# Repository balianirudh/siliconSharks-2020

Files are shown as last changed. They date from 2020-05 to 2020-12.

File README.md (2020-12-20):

# Silicon Sharks ROV 2020

The Silicon Sharks are a high school robotics team that participate in the MATE underwater robotics competition. As a team, our mission is to develop a remotely operated vehicle (ROV) that is capable of exploring public waterways with features for drivers to easily perform tasks and collect data. The five-person team worked together to create this ROV. The Silicon Sharks have three separate subteams (design, electrical, and software) that each played a key role in developing the ROV. My role on the 2020 team was to lead the design and electrical subteams.

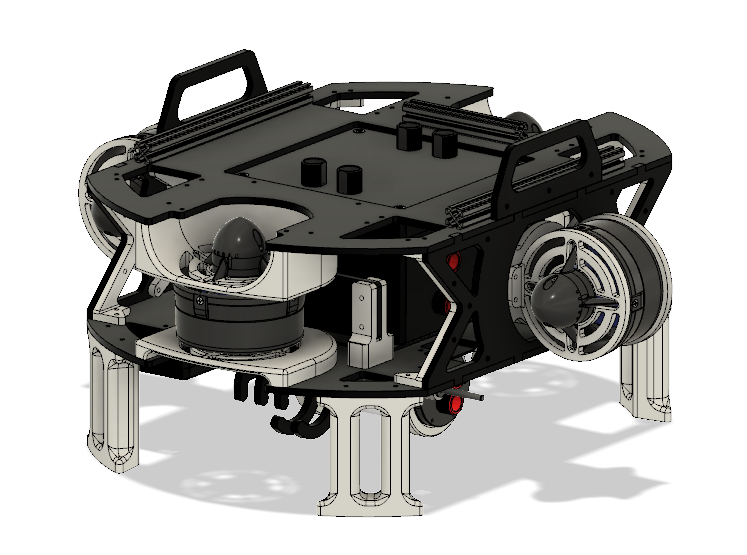
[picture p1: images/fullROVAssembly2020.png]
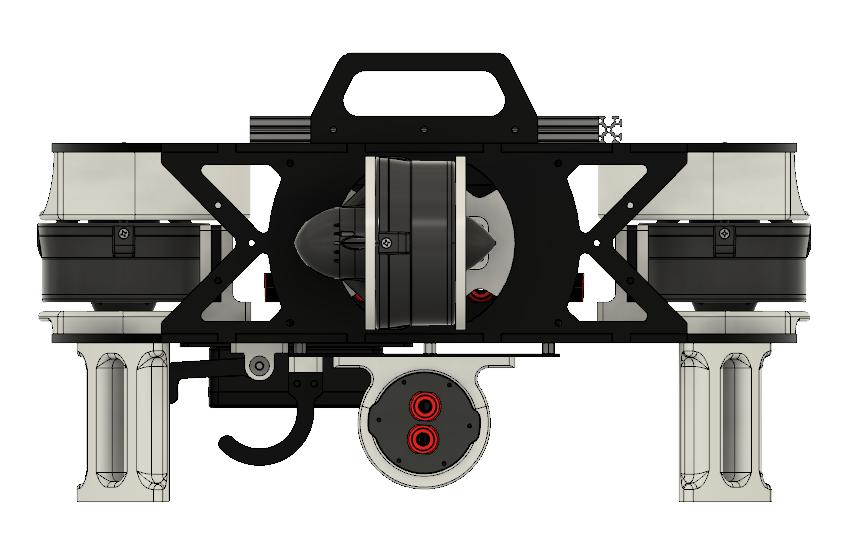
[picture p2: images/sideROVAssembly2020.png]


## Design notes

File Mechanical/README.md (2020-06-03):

# Mechanical Subsystems

The ROV is made up of several mechanical subsystems. The primary mechanical systems of the ROV are the frame, the main electronics
enclosure, the camera enclosures, and the gripper. Our goal was to make a neutrally buoyant, compact, and easily-assembled ROV. To do this, there was a constant emphasis on original design and exploiting custom fabrication.

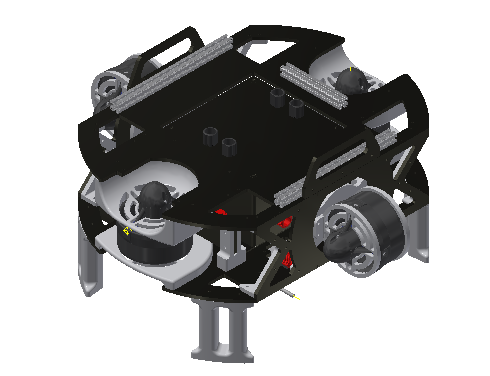
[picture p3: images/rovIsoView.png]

<p align="center"> Isometric View of ROV </p>
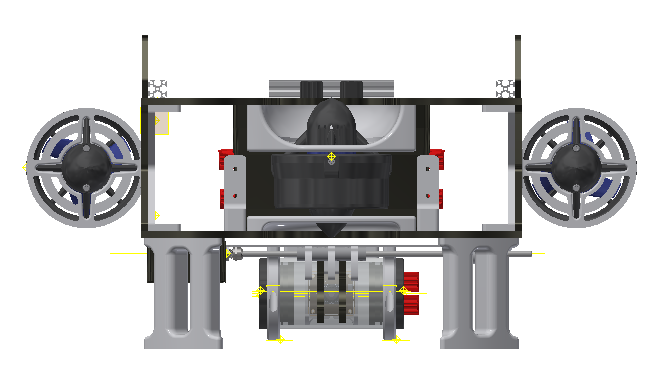
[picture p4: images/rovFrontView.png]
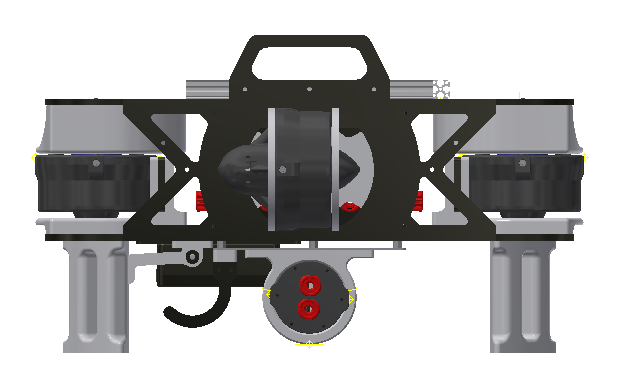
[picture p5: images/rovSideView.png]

<p align="center"> Front View of ROV (left), Side View of ROV (right) </p>

## Frame

When designing the frame of the ROV, the focus was put on creating a high strenth, lightweight, customizable structure with room for adaptability and expasion. The frame was produced thorugh addititive manufacturing (3D printing) due to its rapid prototyping capabilities and ease of customizable. PLA plastic was the primary plastic used for manufacturing because it was a plastic that was not only strong enough, but it is safe to use in underwater applications.

The parts that make up the frame are connected in several ways. The main way is through brackets that are soley meant to bring a general structure to the frame. From here, specific parts such as the main electronics housing or thruster guards reinforce the frame while serving different purposes altogether.

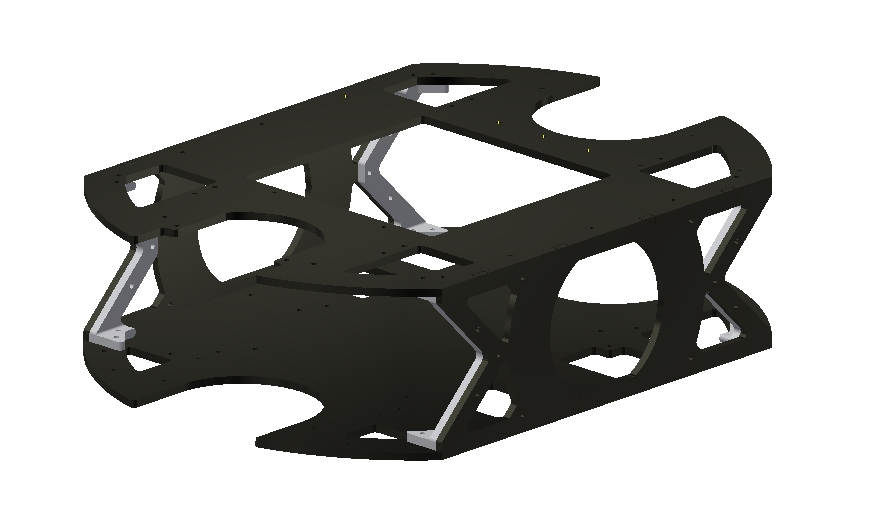
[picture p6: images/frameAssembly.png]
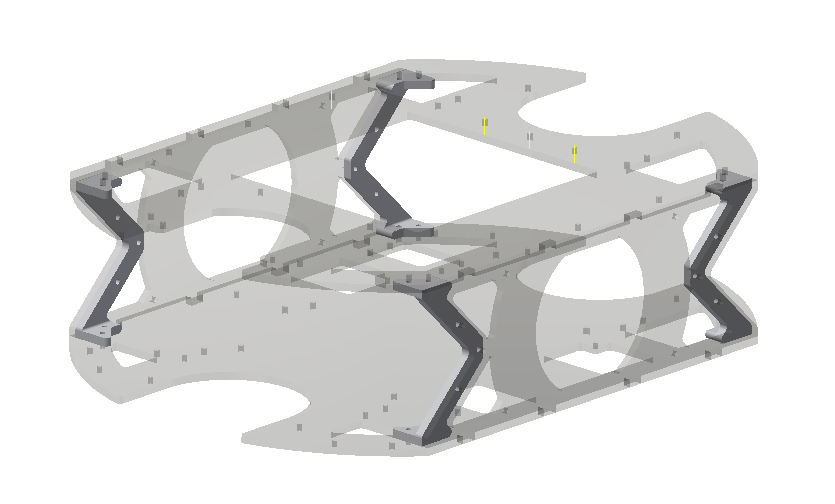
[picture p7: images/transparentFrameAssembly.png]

<p align="center">Frame Assembly</p>

In the process of desiging the frame, considerations had to made for the propulsion of the ROV. The team was constrainted to four thrusters. With these four thrusters, the team had to maximize the ROV's degrees of freedom. The way this was done is discussed in the next section.

## Propulsion

As stated before, the team was constrained to four thrusters. This constraint stems from the regulations of the MATE competition and the thrusters chosen for this ROV. For safety reasons, teams participating in the Ranger class are limited to a 25 amp power supply. The thrusters chosen for this ROV were the Blue Robotics T200 thruster. This thruster was chosen because of its force to current ratio and relative affordability.

"screenshot of force vs current graph of thruster"

Knowing that the power supply can only supply 25 amps, in the electrical design, 20 amps was allocated to the propulsion system. This maximizes the current dedicated to thrusters while leaving enough current for other electrical components and a safety buffer to avoid blowing a fuse. Maximizing the total thrust force is advantageous for obvious reasons. It would provide the maximum agility and make the ROV practical for real-world applications.

The final design was between a three thruster configuration or a four thruster configuration. The team opted for the four thrsuter configuration because of its higher total thrust, but more importantly its symmetry resulting in better controllability. The thruster configuration consists of two thrusters dedicated for vertical movement (z-axis) and two thrusters dedicated for lateral movement (xy plane). This thruster configuration with the thrusters ability to produce a thrust in either direction gives the ROV control over its pitch and yaw. However, the ROV doesn't have explicit control of its roll. Buoyancy foam placed on the top of the ROV keeps it upright and prevents it from rolling. 

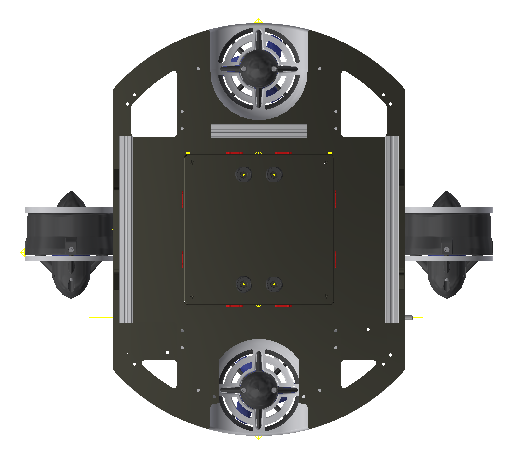
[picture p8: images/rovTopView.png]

<p align="center"> Top View of ROV that highlights thruster configuration</p>

In a future iteration of this ROV, the team plans to gimbal the two thrusters dedicated for lateral movement. This will allow the ROV to move on more complicated paths giving the ROV greater freedom in the water.

## Electronic Enclosures & Sealing

### Main Enclosure

The main electronics enclosure is a diecast aluminum enclosure produced by Polycase. The enclosure is a 6.5in box that houses all the main electronics for communication and thruster control. The diecast aluminum is non-porus and high strength to ensure that the material won't allow water to move into the box over long periods of time submerged in water and won't deform under the water pressures we expect to face.

The electronics within the box are accessed by opening the lid of the enclosure that is held down by four screws. The screws ensure that the lid does not move and keeps the face seal O-ring compressed.

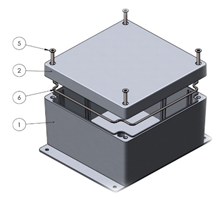
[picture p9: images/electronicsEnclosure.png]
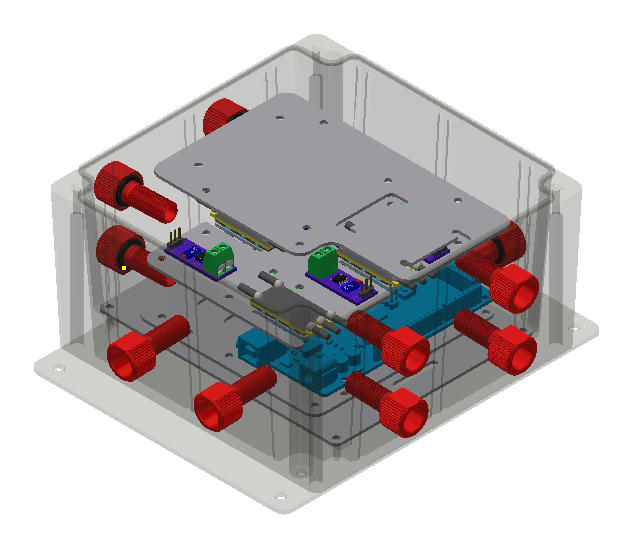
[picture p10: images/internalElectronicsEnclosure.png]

<p align="center"> AN-10F enclosure from Polycase (left), Interior ellectronics enclosure assembly (right) </p>

### Camera Enclosure

The camera enclosure is made up of a clear acrylic tube, two aluminum flanges, and two endcaps. The aluminum flanges allow for the endcaps to mount to the acrylic tube in a way that creates a water-tight seal. Each aluminum flange has two bore O-rings and one face seal O-ring. The acrylic tube compresses the bore O-rings when the flange is inserted and the endcap compresses the face seal O-ring. Clear acrylic tubes were used for the camera enclosures because they make it easy to adjust the camera angle while leaving a wide, unobstructed view for the camera.

"add pictures of camera enclosure"

### Cable Routing

To move cables in and out of the electronics enclosures (with exception to the cameras), aluminum cable penetrators were used. A face seal O-ring on the outside made a water-tight seal with the face of the electronics enclosure while washers inside along with a nut hold the penetrator in place. The cables are secured inside the penetrator with a rubber marine epoxy. This epoxy allows the cable to flex within the penetrator minimizing strain in the cable. The rubber epoxy also ensures no gaps are created by a moving wire.

"add picture of side view of cable penetrator"

For the camera USB cables, submersible grip cords were used to route the cable from the main electronics enclosure to the camera enclosure. Grip cords were used for these specific connections to eliminate the splicing and soldering process that comes with using a regular cable penetrator. Having several solder points in the USB cable was corrupting the camera data so we made a shift to grip cords which solved the problem.

"add picture of grip cord maybe"

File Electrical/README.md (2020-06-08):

# Electrical System

The electrical system consists of the electronics that are used to make the ROV operational. The electrical system is designed to provide 
power and communication for all the sensors and cameras with minimal power consumption and simple circuitry. The ROV is surface powered by a 12-volt external power supply which is then converted to 5V onboard the ROV. The vehicle is controlled by a Logitech gamepad controller through a laptop and the video captured by cameras is displayed on the computer.

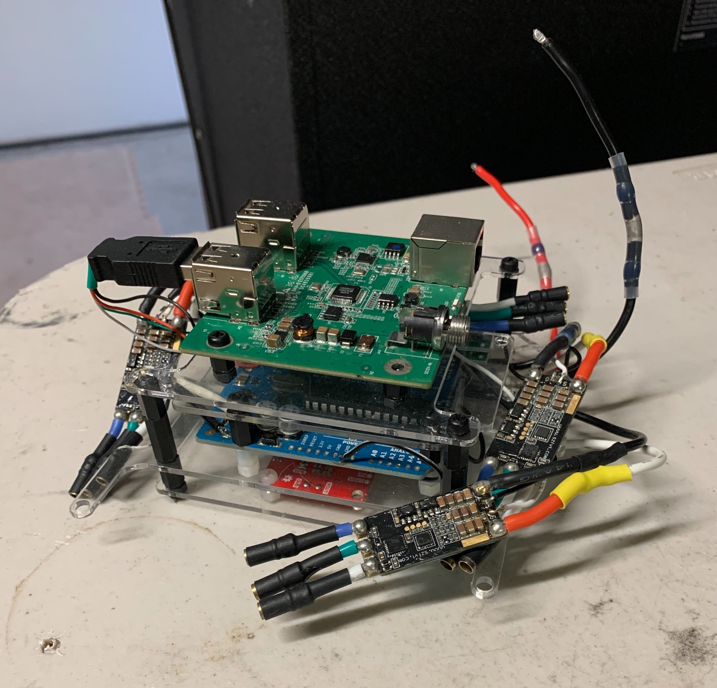
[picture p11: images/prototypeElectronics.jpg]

<p align="center"> Prototype Electronics System </p>

## Power Distribution System

The 12V external power supply is connected directly to the onboard electronics through the ROV's tether. On the tether, there is a 25A fuse to ensure that the electronics are protected if the electronics system tries to draw too much current from the power supply. The 12V is supplied directly to a power distribution module. The power distribution module supplies 12V to each of the thrusters and to the 12V-7.4V buck converter. Along with this, the power distribution module has an integrated 12V-5V converter which supplies a regulated voltage to the microcontroller.

"show picture of power distribution module and servo voltage converter here highlight custom resistor"

The power distribution board chosen for the ROV is the Matek V3.1. This power distribution board was designed for originally designed for quadcopters but can be used in many applications. Because the board was designed for drones, it is very compact making it ideal for out onboard electronics. The features of this board also met our electrical needs as it has an input voltage range of 9V-26V, 4 ESC outputs (each rated to 20A continuous), 5V output (used for the microcontroller), and a 12V output (for the servos). The board is also very affordable making it a good option for the prototype electronics.

The buck converter used to convert 12V to 7.4V is the SparkFun Buck-Boost Converter. This converter was choses because it can convert a 12V input into several different voltages depending on the application. The board was designed for the user to pick a desired output voltage. Based on that voltage, the user solders on a specific resistor to the board (resistance needs to be calculated) which steps down the input voltage to the desired voltage. For this ROV, the serovs operate at 7.4V so a 560Ohm resistor was soldered on to the board to acheive the desired step-down.

"equation to calculate resistance from sparkfun"

## Microcontroller

In the prototype electronics system, an Arduino Uno was used because of its affordabiity as well as its open source AVR microcontroller-based development which can be programmed easily. The Arduino had enough PWM ports to connect all of our thrusters and servos. (add why else we used arduino).
(add documentation about switch to SAM15x15)

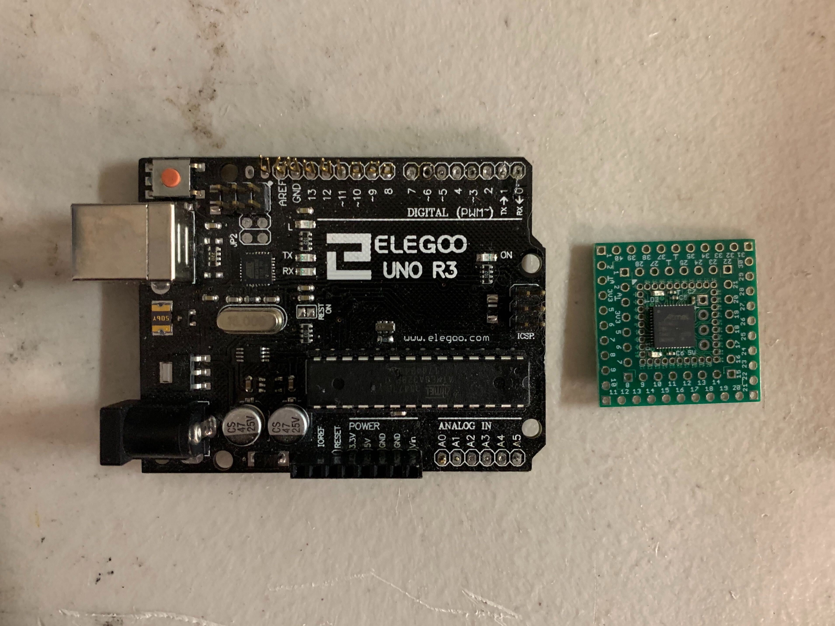
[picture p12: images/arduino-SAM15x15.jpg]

<p align="center"> Side by side comparison of Arduino Uno and SAM15x15 </p>

## Tether

The goal with the tether was to design the most lightweight and thin tether as possible while still satisfying the ROV's electronic demand. The tether encloses just two cables, a power cable and an ethernet cable. The two cables are enclosed in a mesh sheath to keep them together and prevent the cables from tangiling.

"change to better picture of tether"

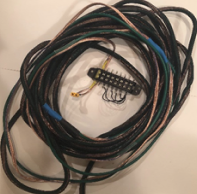
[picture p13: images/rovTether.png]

<p align="center"> ROV Tether </p>

To meet the safety requirements of the MATE competition, the tether has an inline 25A fuse. This protects the electronics onboard the ROV if a thruster or servo draws more current than allocated.

### Communication

Control signals are transmitted from a laptop to the ROV through one Category6 Ethernet cable which has 8 cores. Of the 8 cores, 4 cores are used for serial communication and 4 cores are used for the camera video feed. CAT6 was used as it can provide serial communication at a rate of 250 Kbps.

"add picture of USB to ethernet converters"

### Power

Two 12-gauge wires were used to meet the current rating needed for the ROV. A thicker gauge minimizes the voltage drop from the power supply to the electroncis enclosure. A 12 gauge wire is thick enough to carry a 25A current while keeping the overall tether fairly low profile. To connect to a power supply, the tether has Anderson Powerpole connectors while Wago Lever Nuts connect open leads of the tether to the power distribution board inside the electronics housing. Wago Lever Nuts are using within the enclosure due to their compact size compared to Anderson Powerpole connects or XT60 connectors.

"picture of tether connects" "on pic of wago, highlight open leads of tether and power distribution board"

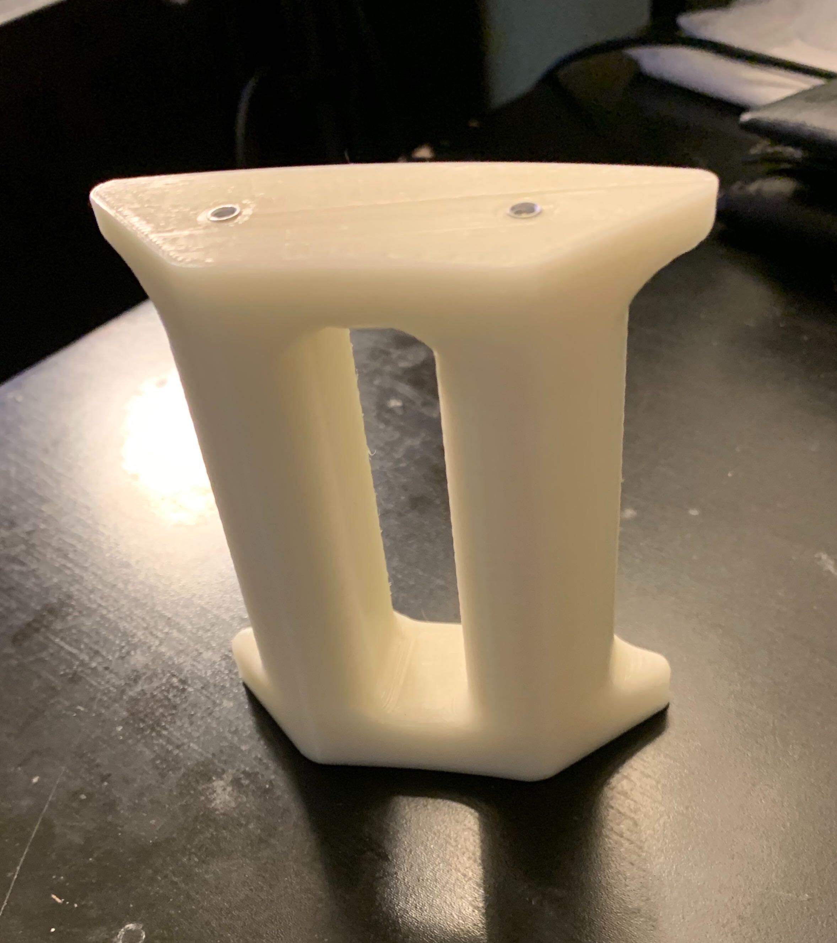
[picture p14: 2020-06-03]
images/rovLandingGear.jpg

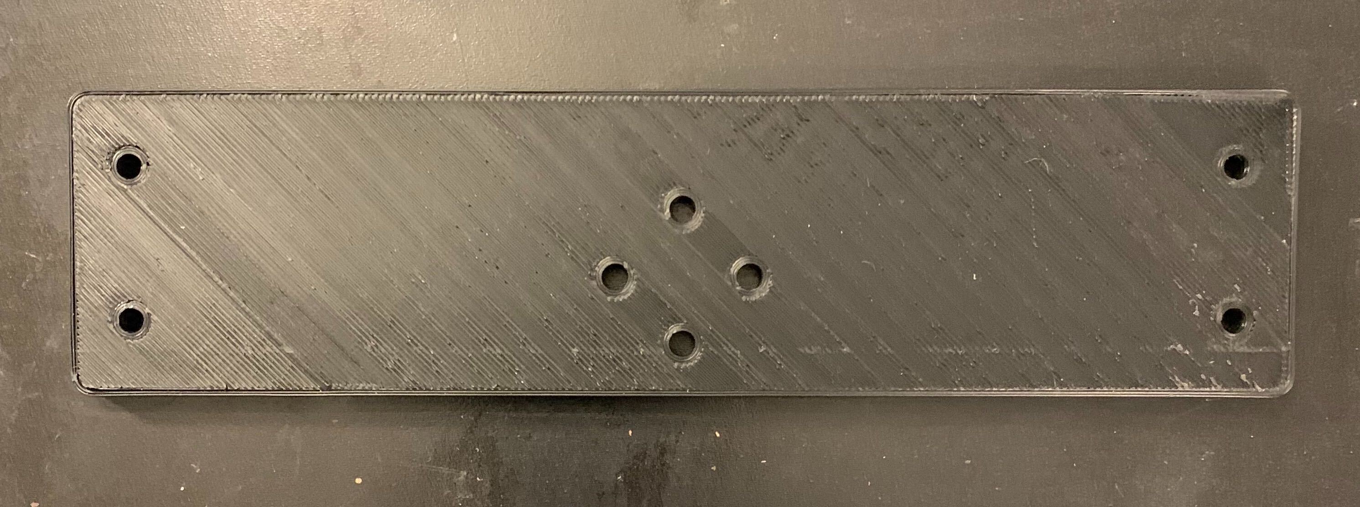
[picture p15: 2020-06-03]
images/verticalThrusterMount.jpg

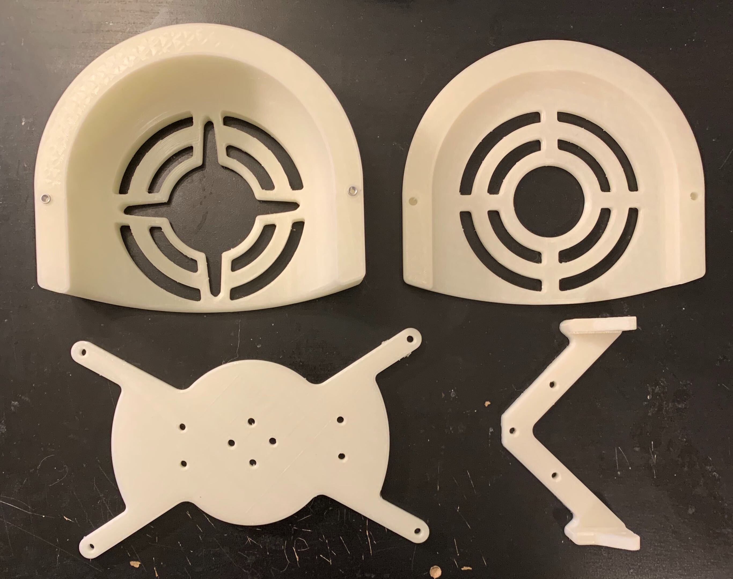
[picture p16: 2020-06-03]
images/3DPrints.jpg

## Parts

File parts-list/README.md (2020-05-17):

All of the parts used to manufacture the 2020 ROV.

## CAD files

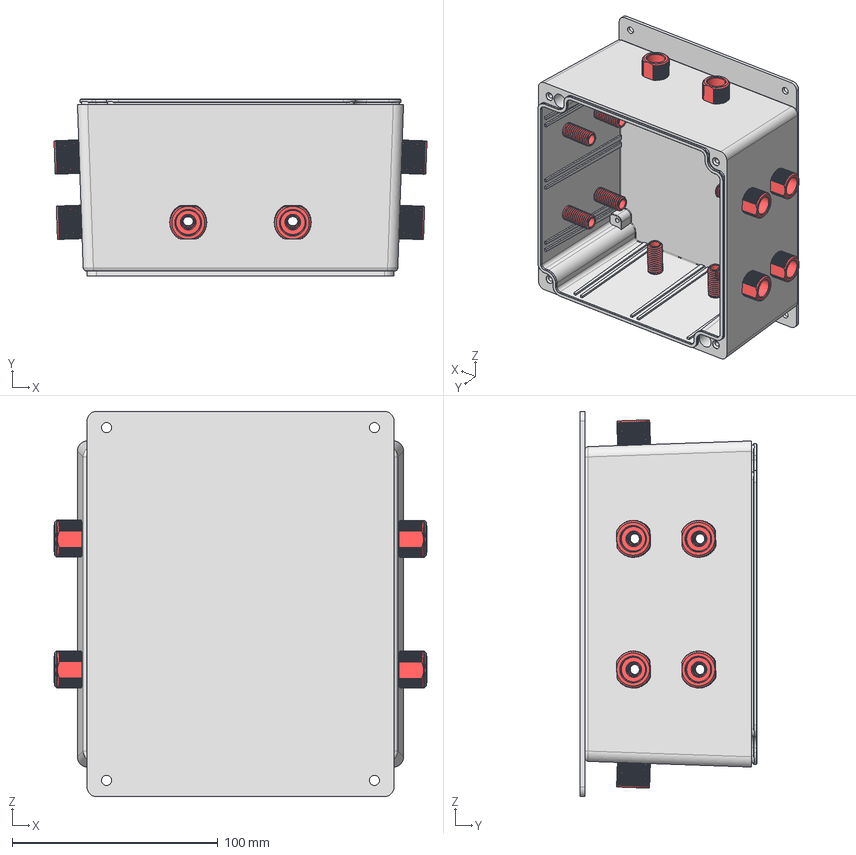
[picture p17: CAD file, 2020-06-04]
Mechanical/CAD/electronicsHousing/mainEnclosure.stp
181.3 x 85.8 x 187.3 mm
AluminumHousing
PENETRATOR-M-BOLT-6MM-10-25-R2 x 12
6mmPenetratorORing x 12

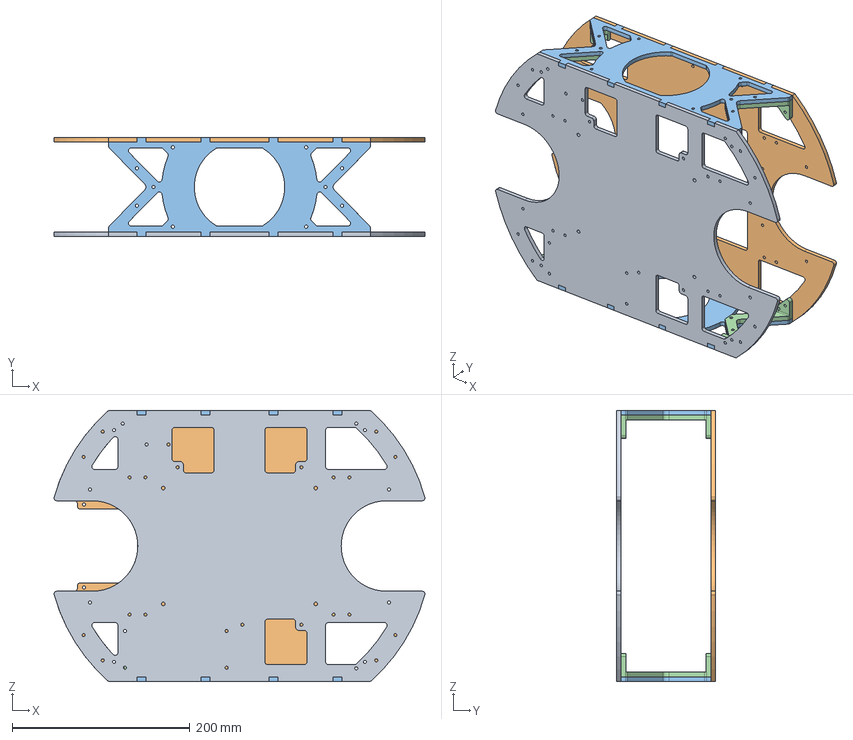
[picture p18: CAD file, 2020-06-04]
Mechanical/CAD/rovAssembly/frameAssembly.stp
417.0 x 111.8 x 304.8 mm
bottomPlate
topPlate
sidePlate x 2
frameBracket x 4

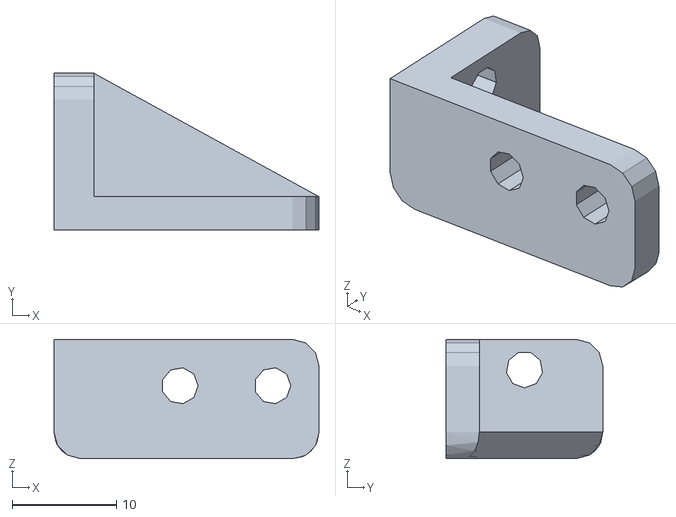
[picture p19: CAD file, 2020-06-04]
Mechanical/CAD/3DPrint/servoMount2.stl
25.4 x 15.0 x 11.4

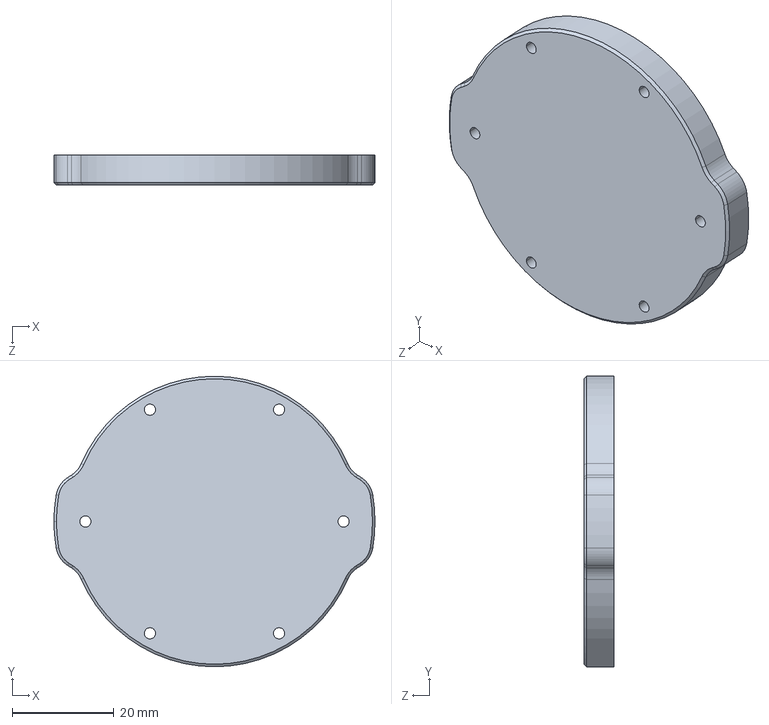
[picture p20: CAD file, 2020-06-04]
Mechanical/CAD/cameraEnclosure/WTE2-M-END-CAP-R1.STEP
63.2 x 57.2 x 6.00 mm

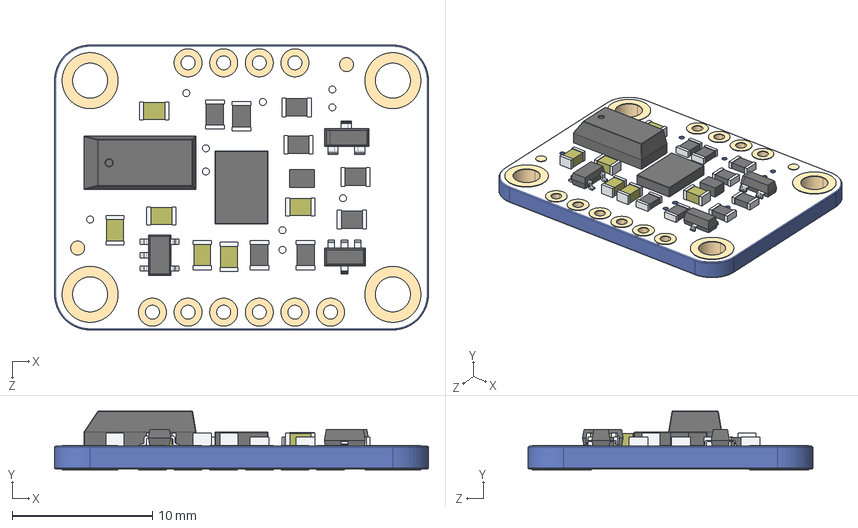
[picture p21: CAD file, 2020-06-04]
Mechanical/CAD/electronicsHousing/Components/Adafruit_BNO055_AP214.STEP
26.7 x 4.20 x 20.3 mm

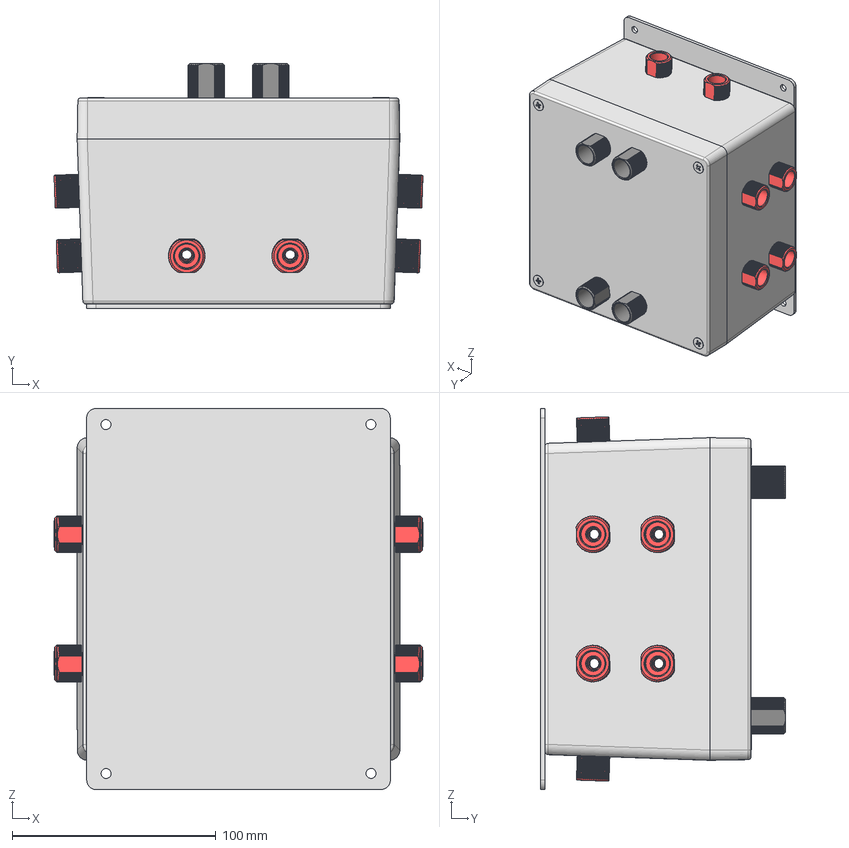
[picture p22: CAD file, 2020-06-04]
Mechanical/CAD/electronicsHousing/ElectricalHousing2.stp
181.3 x 120.6 x 187.4 mm
AluminumHousing
PENETRATOR-M-BOLT-6MM-10-25-R2 x 12
6mmPenetratorORing x 16
PENETRATOR-M-BOLT-8MM-10-25-R1 x 4

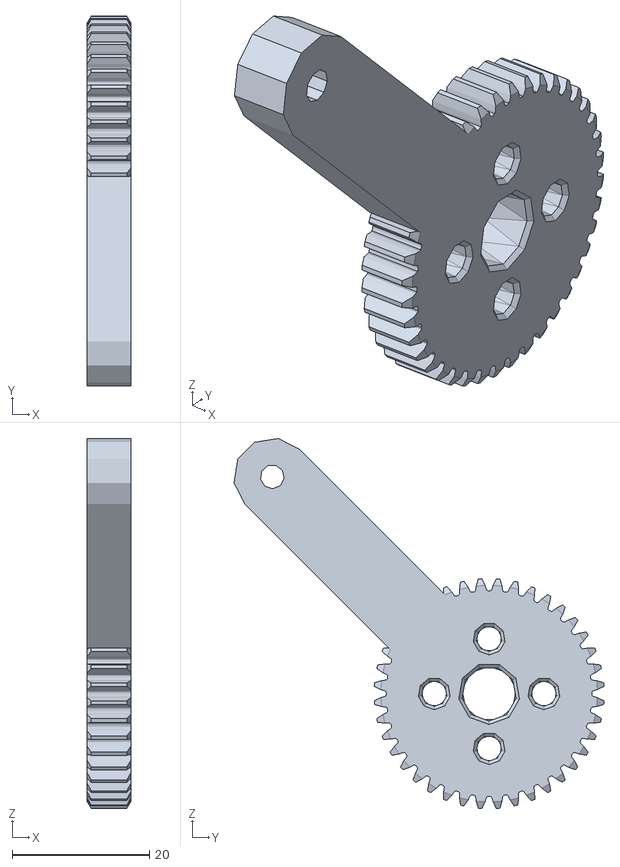
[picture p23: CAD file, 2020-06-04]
Mechanical/CAD/3DPrint/gripperPart1.stl
6.35 x 54.0 x 54.0

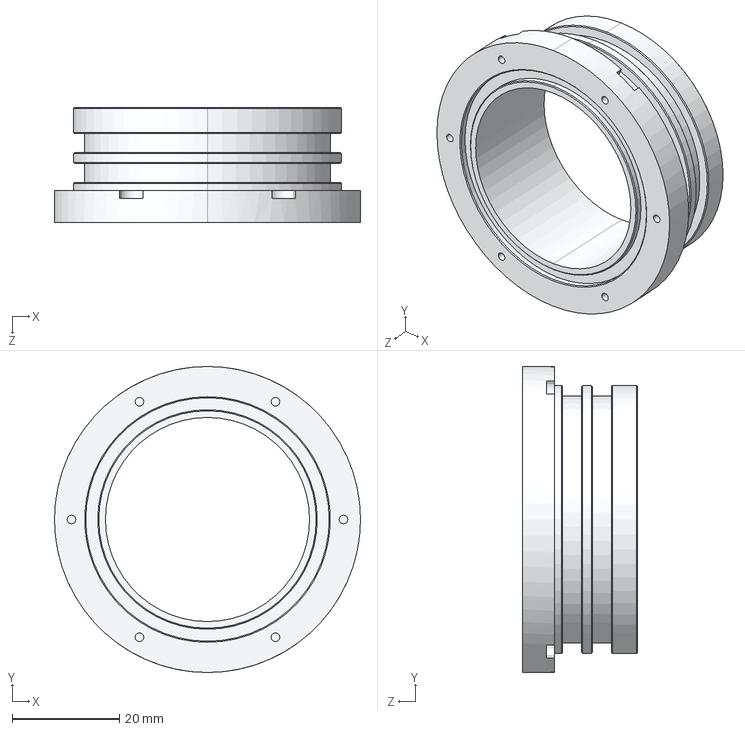
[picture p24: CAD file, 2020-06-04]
Mechanical/CAD/cameraEnclosure/WTE2-M-FLANGE-SEAL-R4.STEP
57.2 x 57.2 x 21.5 mm

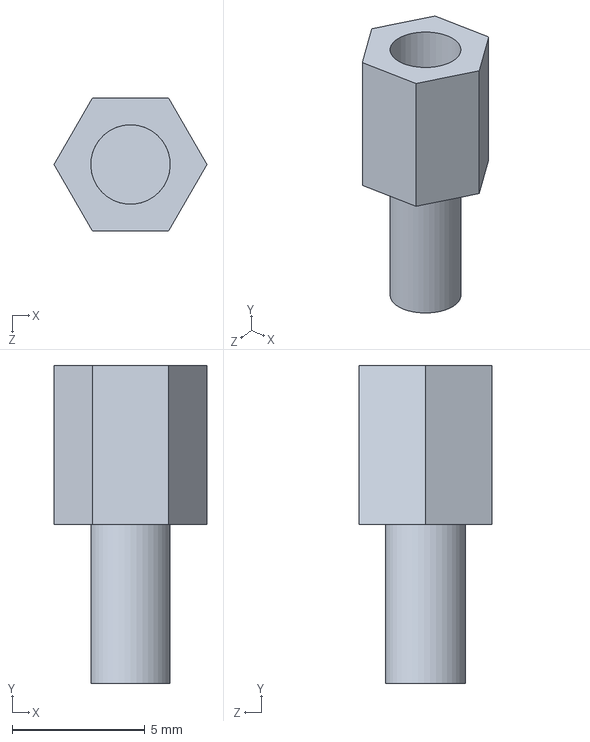
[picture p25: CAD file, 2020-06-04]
Mechanical/CAD/electronicsHousing/Components/Separador plastico negro H-M M3x6x6mm.SLDPRT
5.77 x 12.0 x 5.00 mm

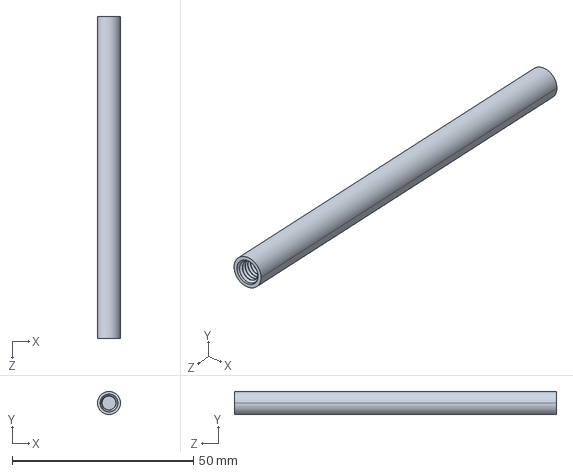
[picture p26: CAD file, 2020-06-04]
Mechanical/CAD/rovAssembly/THRDED ROUND STANDOFF.STEP
6.35 x 6.35 x 88.9 mm

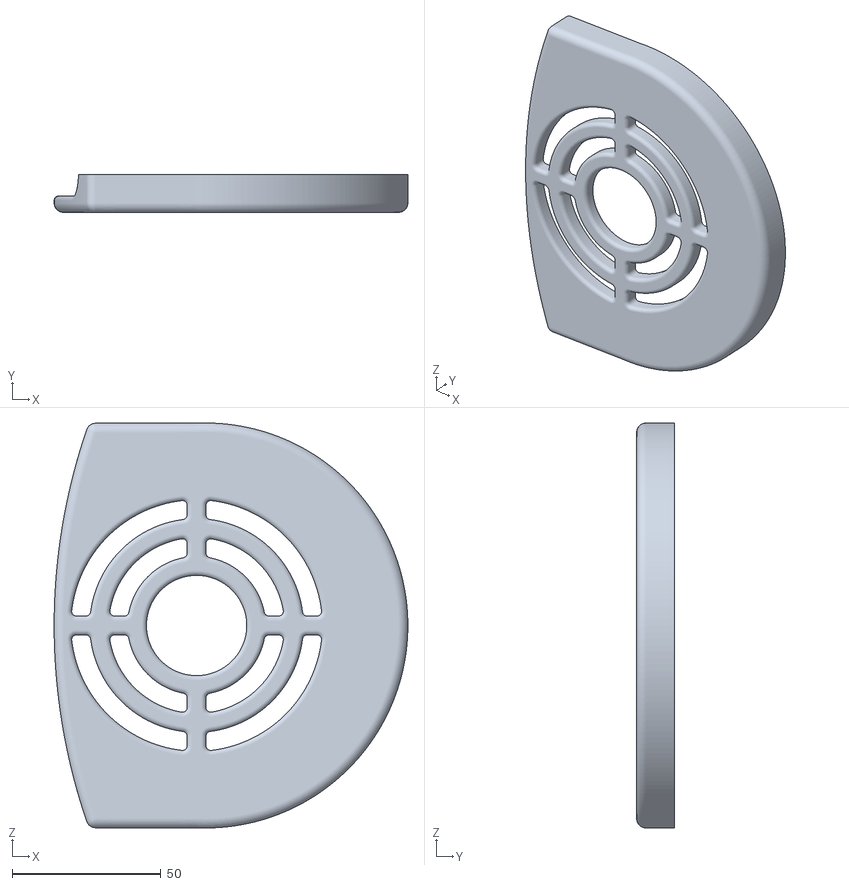
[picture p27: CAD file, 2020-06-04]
Mechanical/CAD/3DPrint/bottomThrusterCover.stl
118.8 x 12.7 x 136.0

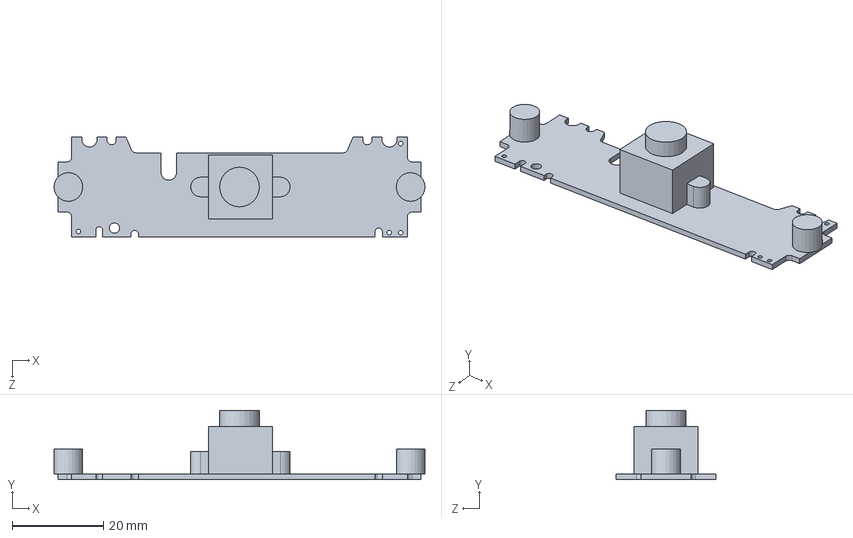
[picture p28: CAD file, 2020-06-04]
Mechanical/CAD/cameraEnclosure/logitech_camera.SLDPRT
81.3 x 15.2 x 22.0 mm

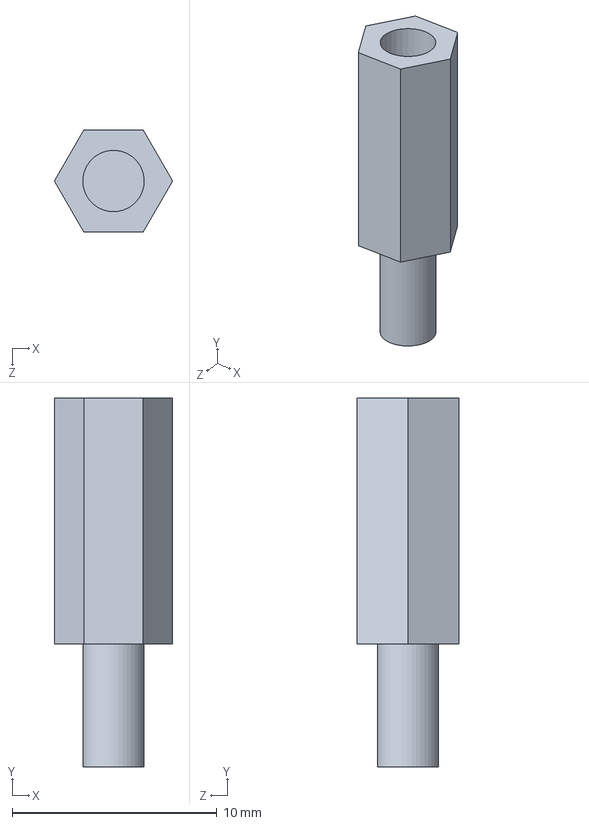
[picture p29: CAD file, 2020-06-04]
Mechanical/CAD/electronicsHousing/Components/Separador plastico negro H-M M3x12x6mm.SLDPRT
5.77 x 18.0 x 5.00 mm

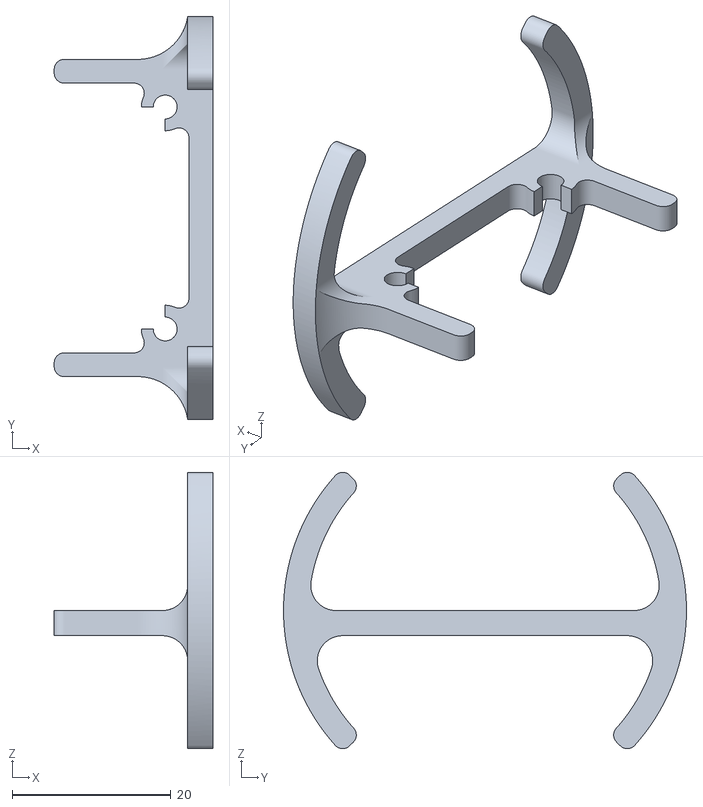
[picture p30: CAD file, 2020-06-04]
Mechanical/CAD/3DPrint/cameraMount2.stl
20.0 x 50.8 x 34.8

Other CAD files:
Mechanical/CAD/cameraEnclosure/CameraEnclosure1.stp
Mechanical/CAD/electronicsHousing/Components/Separador plastico negro H-M M3x10x6mm.SLDPRT
Mechanical/CAD/3DPrint/servoMount.stl
Mechanical/CAD/cameraEnclosure/WTE2-P-TUBE-12-R1.STEP
Mechanical/CAD/3DPrint/acrylicMount.stl
Mechanical/CAD/3DPrint/axleMount.stl
Mechanical/CAD/3DPrint/backSideThrusterCover.stl
Mechanical/CAD/3DPrint/cameraMount3.stl
Mechanical/CAD/3DPrint/frameBracket.stl
Mechanical/CAD/3DPrint/frontSideThrusterCover.stl
Mechanical/CAD/3DPrint/gripperPart2.stl
Mechanical/CAD/3DPrint/gripperPart3.stl
Mechanical/CAD/3DPrint/gripperPart4(mm).stl
Mechanical/CAD/3DPrint/gripperPart4.stl
Mechanical/CAD/3DPrint/handle.stl
Mechanical/CAD/3DPrint/newEndCap.stl
Mechanical/CAD/3DPrint/optimizedlandingGear v6.stl
Mechanical/CAD/3DPrint/sidePlate.stl
Mechanical/CAD/3DPrint/thrusterMounrt.stl
Mechanical/CAD/3DPrint/topThrusterCover.stl
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

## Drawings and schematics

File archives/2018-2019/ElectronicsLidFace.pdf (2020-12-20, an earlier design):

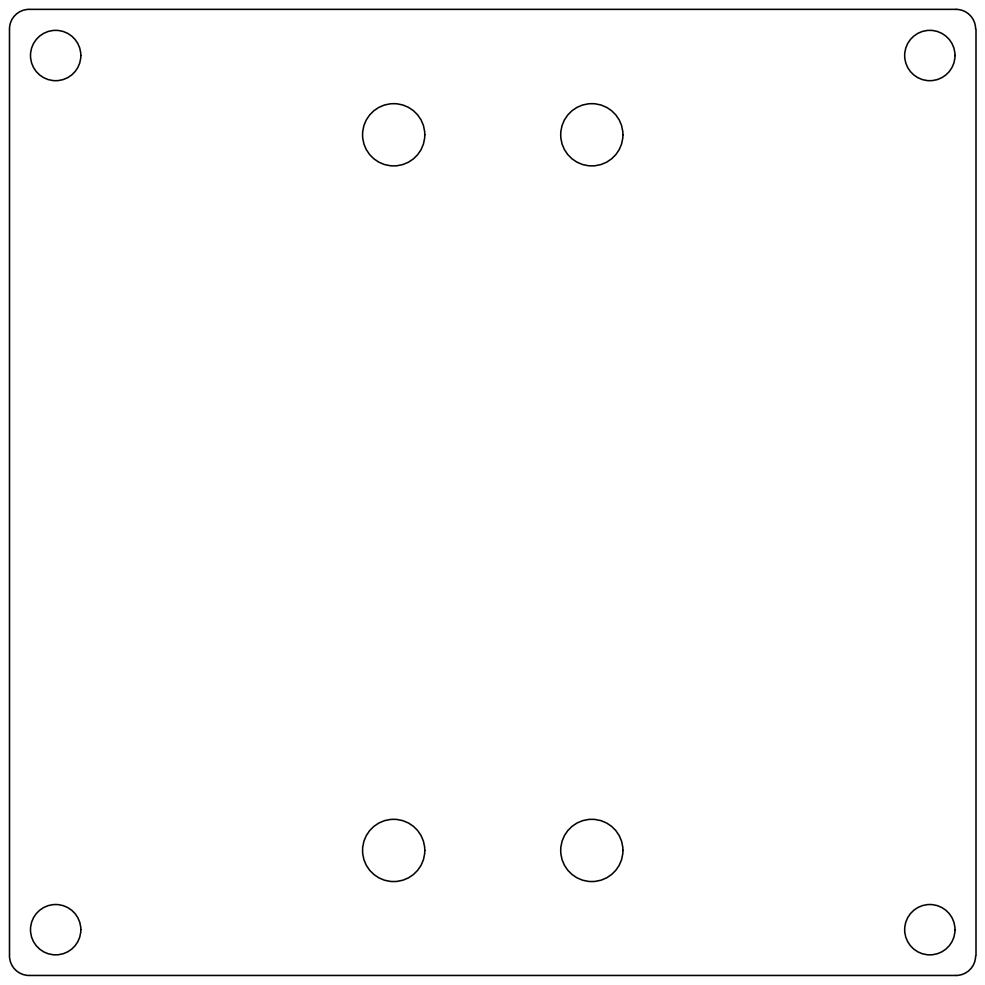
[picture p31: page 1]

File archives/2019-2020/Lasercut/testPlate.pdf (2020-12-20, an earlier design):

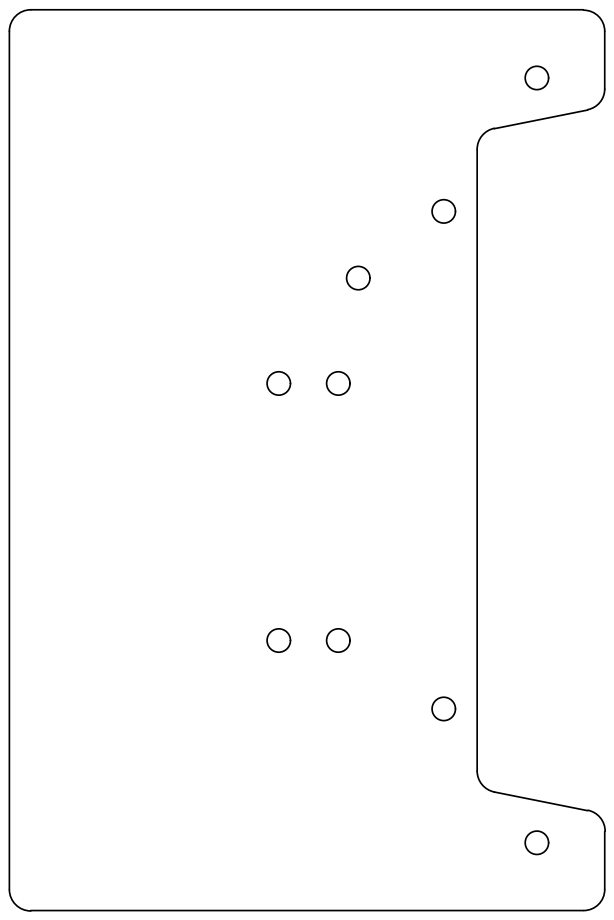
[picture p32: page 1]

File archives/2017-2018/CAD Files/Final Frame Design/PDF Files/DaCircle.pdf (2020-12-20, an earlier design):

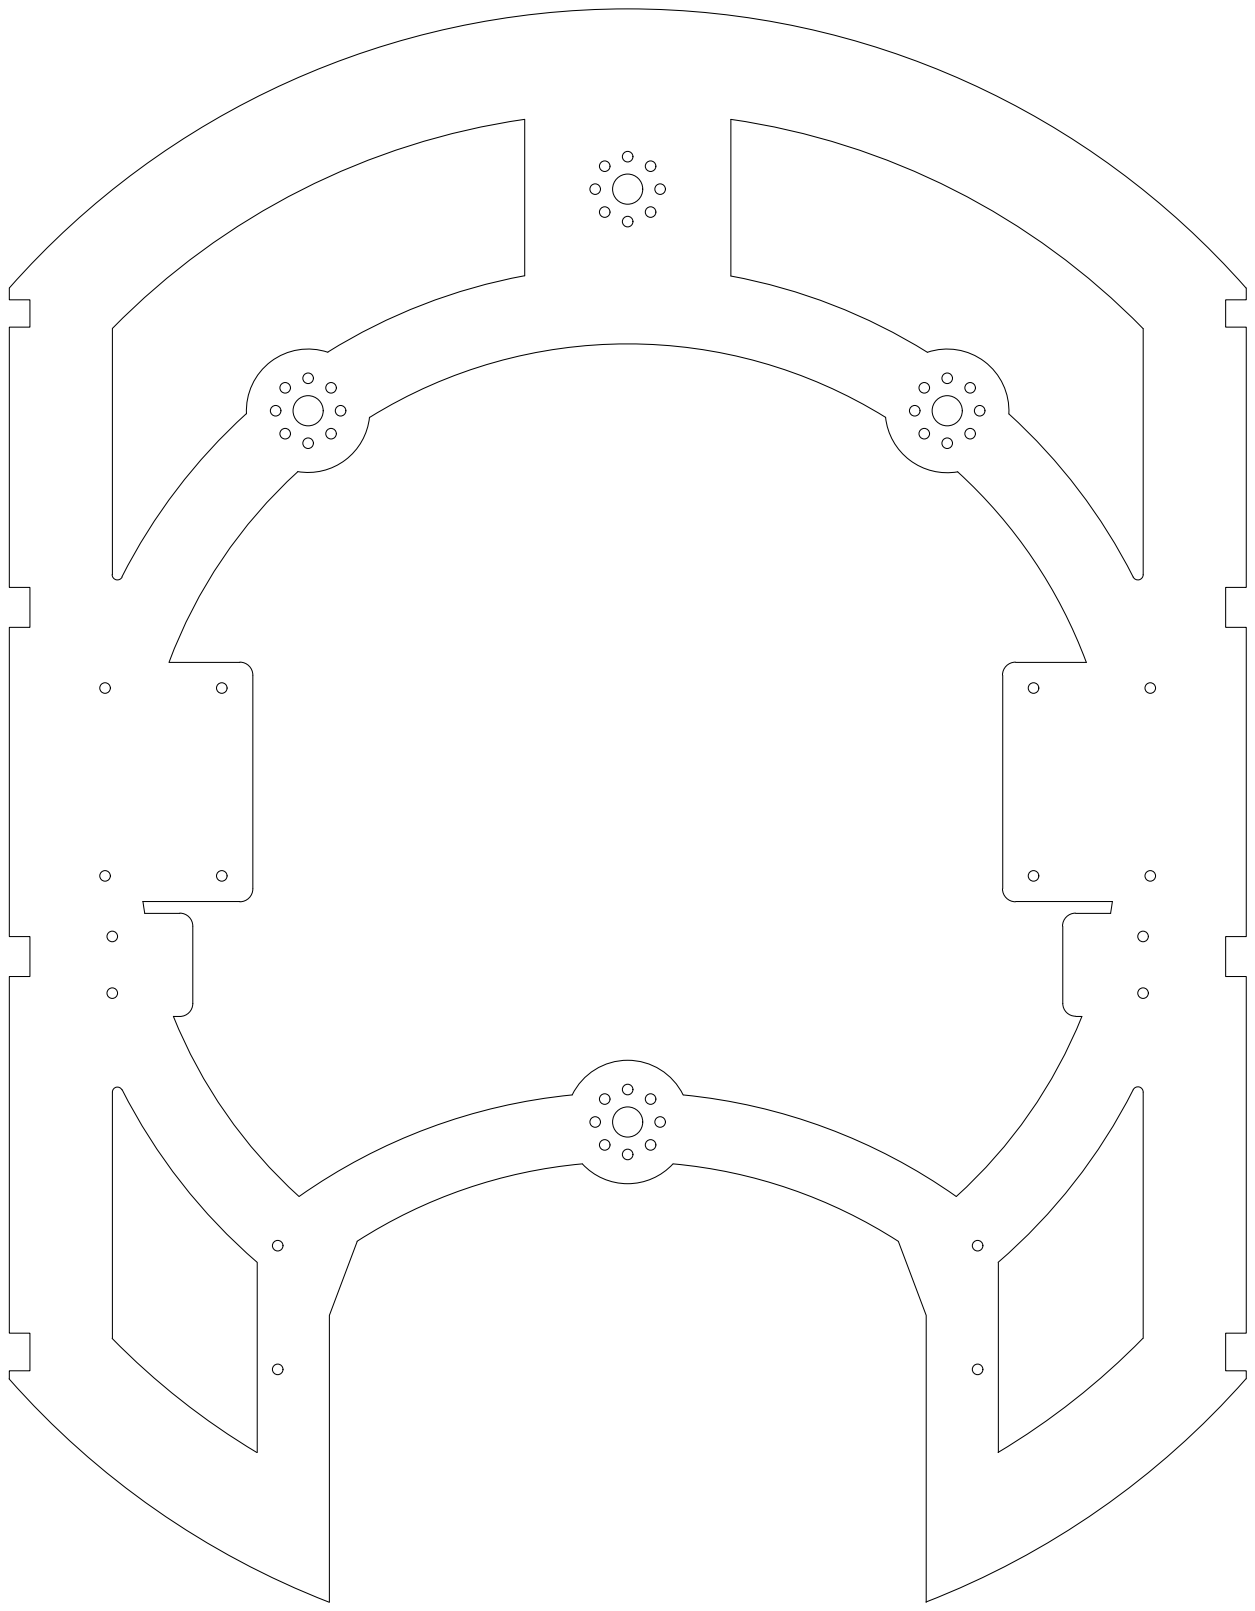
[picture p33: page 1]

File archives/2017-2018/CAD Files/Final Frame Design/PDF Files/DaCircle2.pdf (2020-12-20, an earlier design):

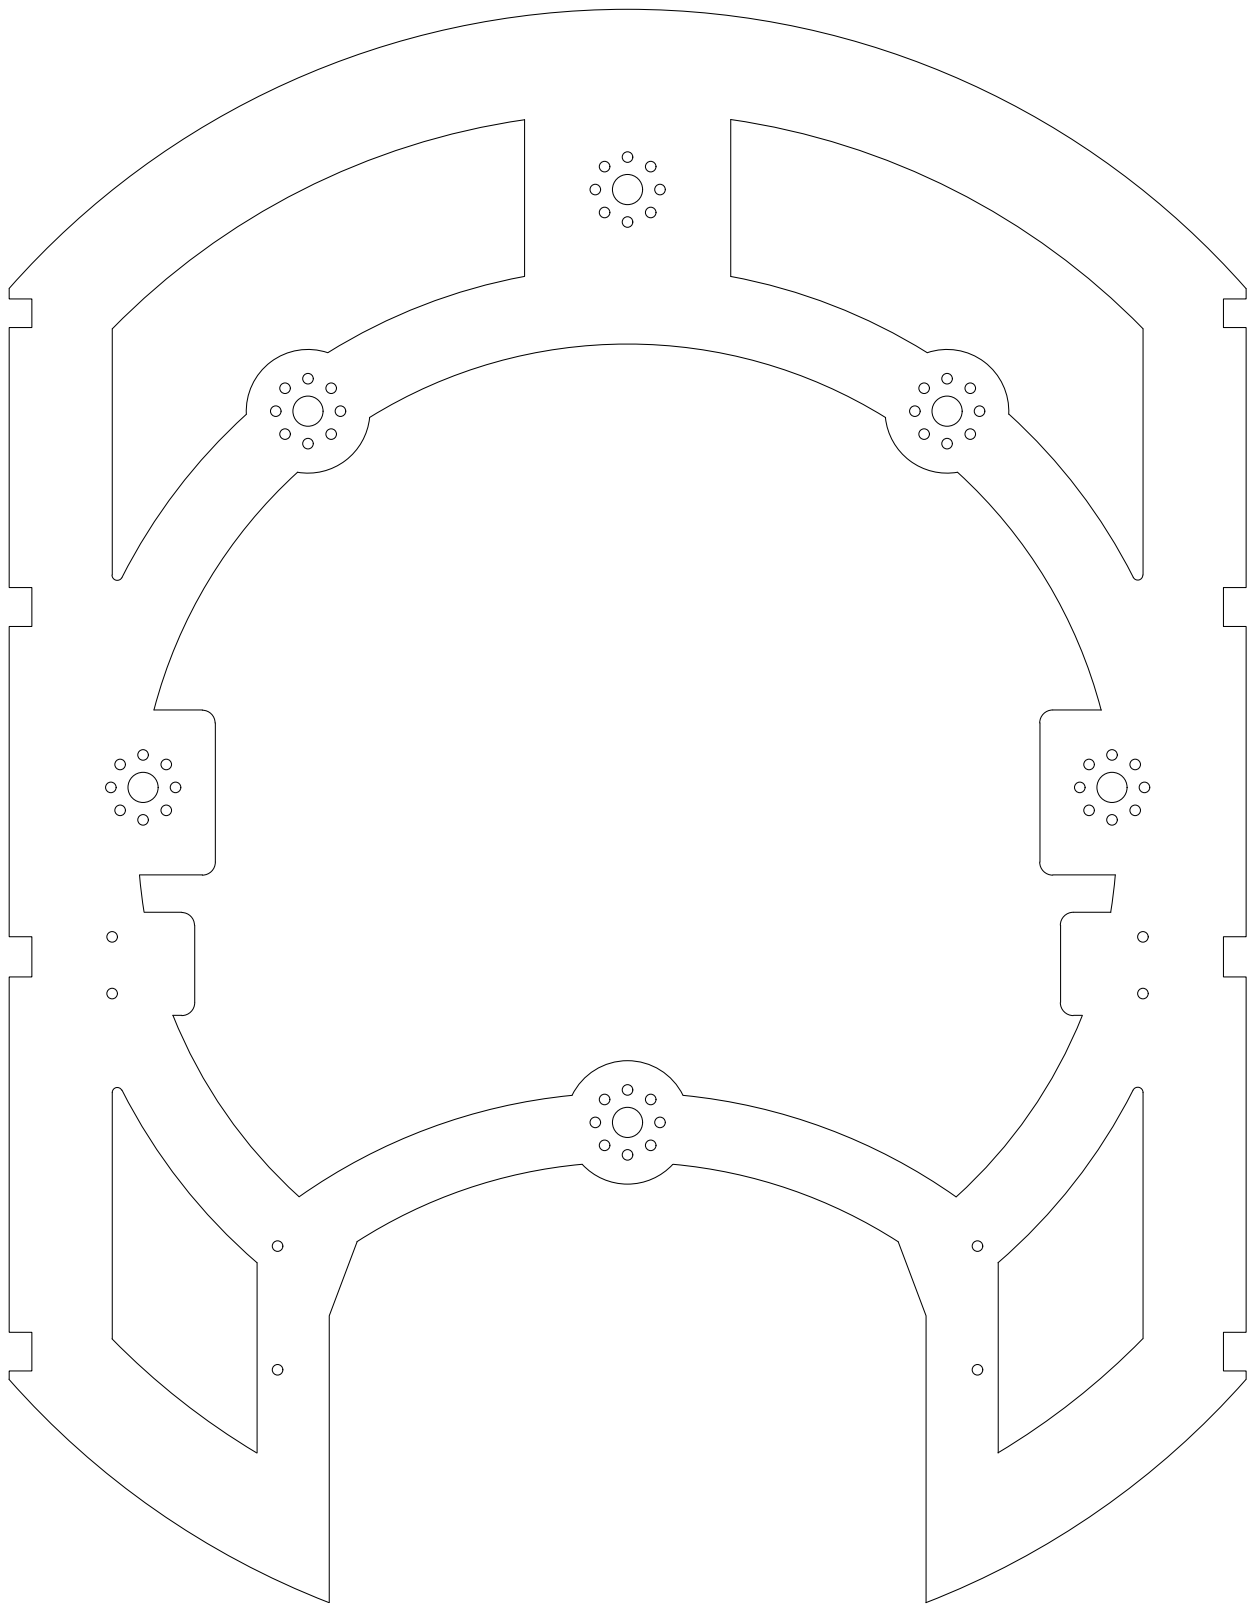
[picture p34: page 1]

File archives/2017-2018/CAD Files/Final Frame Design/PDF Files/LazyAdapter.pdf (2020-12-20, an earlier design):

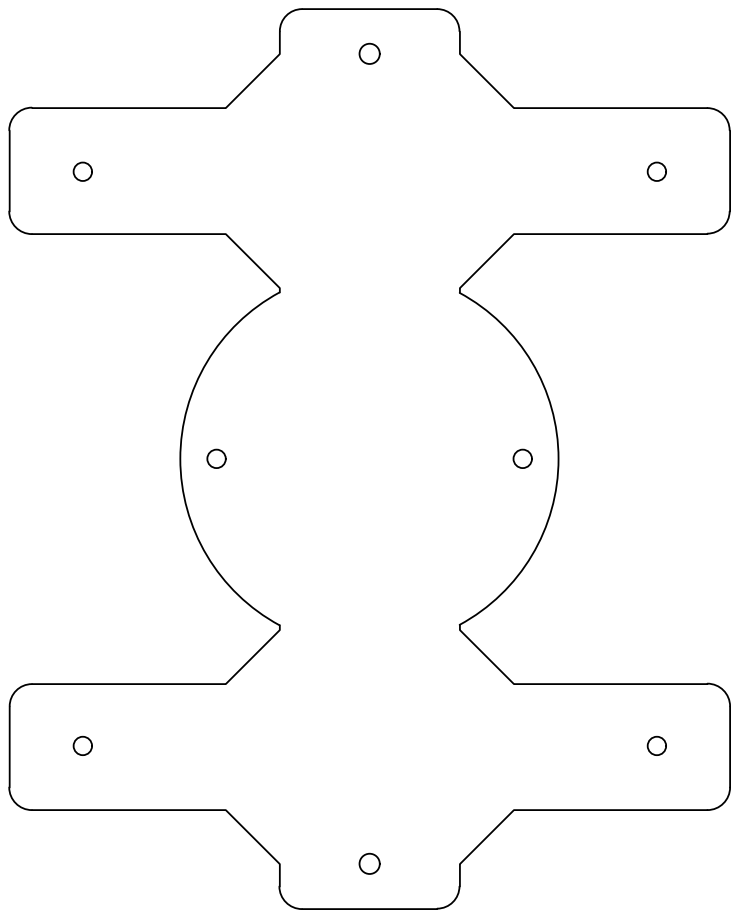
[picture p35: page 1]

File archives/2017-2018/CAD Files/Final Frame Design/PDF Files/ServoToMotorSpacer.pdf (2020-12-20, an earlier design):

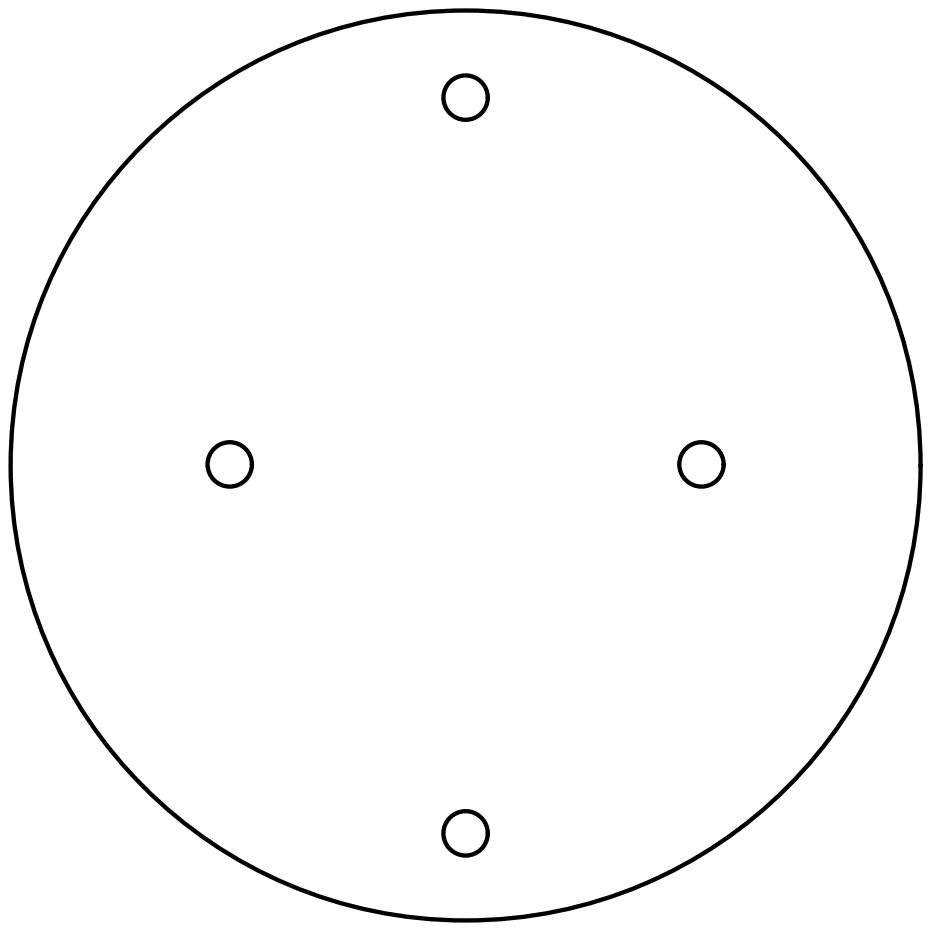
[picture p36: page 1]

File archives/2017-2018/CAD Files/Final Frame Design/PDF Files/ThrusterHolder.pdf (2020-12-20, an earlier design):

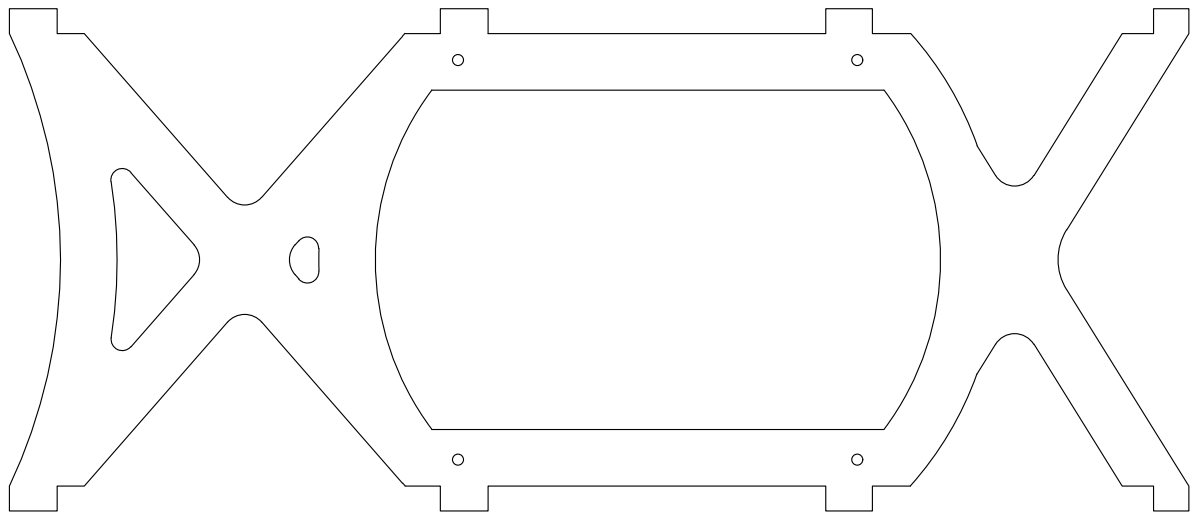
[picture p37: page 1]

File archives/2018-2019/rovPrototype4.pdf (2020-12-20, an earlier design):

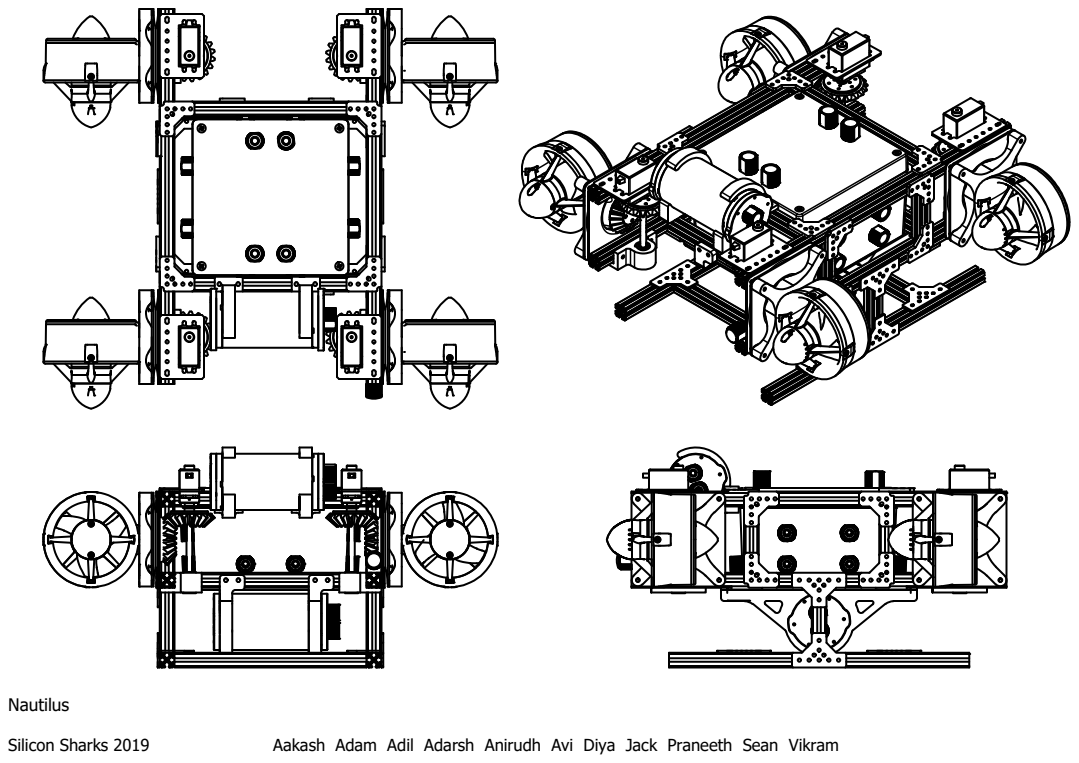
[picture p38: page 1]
Silicon Sharks 2019; Aakash Adam Adil Adarsh Anirudh Avi Diya Jack Praneeth Sean Vikram

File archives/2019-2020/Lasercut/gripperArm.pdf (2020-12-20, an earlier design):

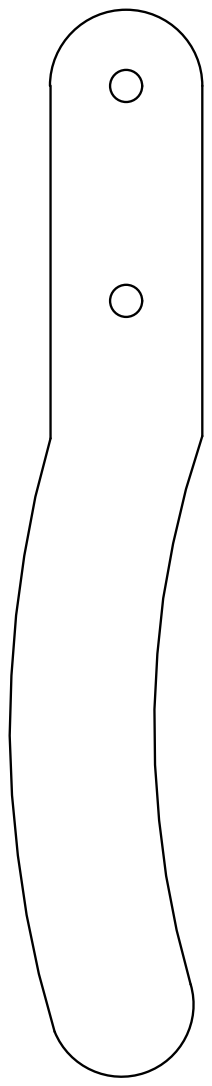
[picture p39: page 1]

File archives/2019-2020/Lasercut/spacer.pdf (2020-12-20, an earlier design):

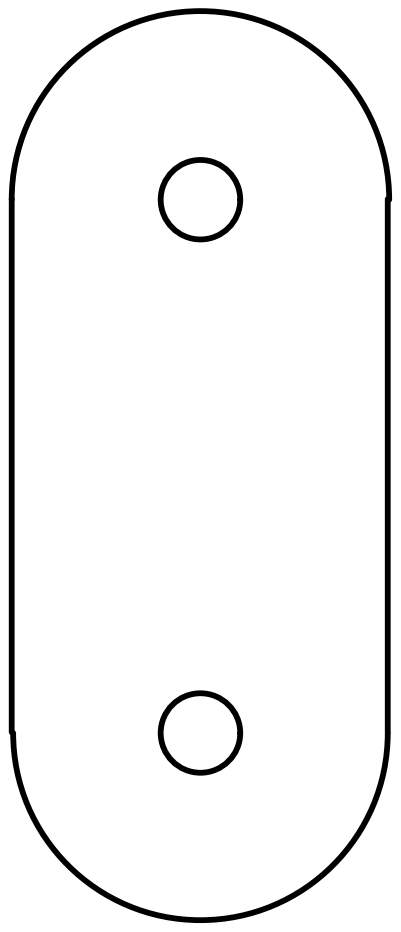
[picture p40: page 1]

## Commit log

2020-05-21 Updated electronics enclosures documentation
2020-05-27 Updated information on power distribution
2020-06-04 Need to add servo box files
2020-06-08 Added power distribution documentation
